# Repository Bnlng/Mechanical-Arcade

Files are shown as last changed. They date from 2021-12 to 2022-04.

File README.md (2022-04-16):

<h1>Mechanical Dogfight</h1>
<h3>Von Ben und Martin, 12bc</h3>

<h2>Inhaltsverzeichnis</h2>

<ul style="list-stlye-type:none">
    <li><a href="#einl">1. Einleitung</a></li>
    <li><a href="#proj">2. Das Projekt</a></li>
    <li><a href="#hard">3. Hardware</a></li>
    <ul>
        <li><a href="#aufb">3.1 Aufbau</a></li>
        <li><a href="#teil">3.2 Verwendete Bauteile</a></li>
        <li><a href="#schalt">3.3 Schaltplan</a></li>
    </ul>
    <li><a href="#soft">2. Software</a></li>
</ul>

<h2 id="einl">Einleitung</h2>

Dies ist die Projektseite für unser Informatikprojekt des ersten Halbjahres. Uns war von Anfang an klar, dass wir etwas im Bereich des Physical Computing machen wollen. Als wir einen alten Joystick aus den 90er Jahren auf dem Dachboden gefunden hatten sind wir auf die Idee für dieses Projekt gekommen und waren sofort begeistert. Wir haben uns dazu entschieden, das Projekt auf der Arduino Plattform umzusetzen, da diese recht einsteigerfreundlich und Perfekt für Projekte wie dieses geeignet ist.
    
<h2 id="proj">Das Projekt</h2>

"Mechanical Dogfight" ist ein Singleplayer Computerspiel auf Arduino-Basis, dessen Inhalt ein Luftkampf (engl. Dogfight) zwischen zwei Flugzeugen ist. Der Spieler steuert das Verfolgerflugzeug, eine englische Supermarine Spitfire, mit einem Joystick. Das Besondere an diesem Spiel ist, dass es sich nicht auf einem Bildschirm abspielt, sondern mit echten Modellen der Flugzeuge, welche sich zweidimensional im Spielekasten bewegen können. Das Gegnerflugzeug wird automatisch vom Arduino gesteuert und muss vom Spieler mittels des Bordgeschützes getroffen werden. Zurzeit ist nur das Flugzeug des Spielers fertiggestellt, daher handelt es sich bei diesem Projekt erst einmal nur um eine Art „Proof of Concept“. Alles funktioniert, wie gedacht, weshalb wir das Projekt als vollen Erfolg ansehen. Wer das Projekt in Bewegung sehen möchte kann es sich [hier](https://www.youtube.com/watch?v=7guUQbI5MUM) aus der Sicht des Spielers anschauen und [hier](https://www.youtube.com/watch?v=KiZhklhcncI) von hinten, wobei auch die Mechanik des Spiels zu sehen ist.



<h2 id="hard">Hardware</h2>

<h3 id="aufb">Aufbau</h3>

Damit das Flugzeug alle Punkte erreichen kann haben wir zweiachsiges mechanisches Bewegungssystem gebaut. Es basiert auf zwei Schlitten, welche sich jeweils waagerecht und senkrecht in Schienen bewegen. Die Bewegung wird durch zwei Getriebemotoren ermöglicht, welche die Rotation mittels Zahnräder und Zahnstangen in lineare Bewegung auf die Schlitten übertragen. Der komplette Aufbau für die senkrechte Bewegung ist auf dem Schlitten für die Waagerechte Bewegung montiert. Der Aufbau und die Funktion werden verständlicher bei Betrachtung des folgenden Bildes und des 3D-Modelles (zu öffnen mit 3D-Viewer, bei Windows 10 vorinstalliert).
 


Ein genaueres 3D Modell kann unter <code>3D Modell.3mf</code> in den Dateien des Repositorys eingesehen werden.

Außerdem findet sich [hier](https://www.youtube.com/watch?v=KiZhklhcncI) ein Vorführungsvideo aus der Ansicht von hinten, also vom späteren Inneren des Spielekastens. [Hier](https://www.youtube.com/watch?v=7guUQbI5MUM) findet sich ein Vorführungsvideo aus der Spieleransicht.

<h3 id="teil">Verwendete Bauteile</h3>

<h4>Netzteil 7-9V</h4>

Dieses versorgt den Arduino und die Motoren mit Strom. Der Arduino Nano benötigt eine Spannungsversorgung von 7 bis 12V um arbeiten zu können. Eine besonders hohe Leistung muss das Netzteil nicht aufweisen, da das gesamte Projekt noch keine Ströme über 1A gezogen hat.

<h4>Arduino</h4>

Arduino ist eine Open Source Physical-Computing-Plattform. Es handelt sich um einen Microcontroller mit mehreren analogen und digitalen Ein und Ausgängen. Dieser ist das Herzstück unseres Projektes und für die Verarbeitung der Steuersignale und später für das Steuern des Gegnerflugzeuges und das Punktezählen zuständig.

<h4>DC-Motor-Treiber</h4>
Hierbei handelt es sich um den L298N dual H-Bridge Driver. Dieser ermöglicht die Steuerung von zwei Gleichstrommotoren. Also die Änderung von Drehrichtung und Geschwindigkeit.

<h4>DC-Getriebemotoren</h4>

Diese sind für die Bewegung des Flugzeuges zuständig. Durch das Getriebe sind sie in der Lage deutlich mehr Drehmoment zu leisten. Dies ist für das Projekt notwendig, da die Motoren sonst nicht in der Lage wären auch nur eine Umdrehung zu machen.  

<h4>3D-Gedruckte Komponenten</h4>

Alle, im oben zu sehenden 3D-Modell schwarz gefärbten Komponenten sind mittels einem FDM Druckers aus PLA gefertigt worden. Die Hauptkomponenten sind die zwei Schlitten, auf denen die Motoren und das Flugzeug montiert sind, sowie die Zahnräder und Zahnstangen für die Kraftübertragung des Motors.  Die Teile wurden von uns selbst in dem CAD-Programm <I>Fusion 360</I> entwickelt.  Nur das Flugzeugmodell ist ein 3D-Scan aus dem Internet, jedoch musste hier die Einbettung für den Laserpointer in den Rumpf modelliert werden.

<h4>Schubladenschienen</h4>

Die Schienen, auf denen sich die Schlitten bewegen sind die äußeren Schienen von Kugelauszügen. Diese haben links und rechts an der Innenseite eine halbkreisförmige Nut. Diese Nuten bilden die einzige Kontaktfläche zwischen Schlitten und Schiene. Den inneren Teil des Kugelauszuges dienen zur Stabilisierung der Zahnstangen, welche aufgrund der Abmessungen in zwei Teilen gedruckt werden mussten.

<h4>Joystick</h4>

Bei dem Joystick handelt es sich um einen Logitech Wingman Extreme aus dem Jahre 1994. Die Ermittlung der Stellung erfolgt mittels zwei Drehpotentimetern, eines für die X-Achse und eines für die Y-Achse. Potentiometer sind Spannungsteiler. An zwei der drei Anschlüsse wird eine Spannung angelegt, an dem dritten Anschluss ist nun abhängig vom Winkel der Drehachse eine Spannung messbar. Diese Spannung dient dem Arduino als Inputwert für die Bewegung des Flugzeuges.

<h4>Taster</h4>

An jedes Ende der Bewegungsachsen ist ein Taster montiert, welcher gedrückt wird, wenn die Bewegungsschlitten an das Ende der Bewegungsachsen stoßen. Wir haben Taster mit Rollenhebel genutzt, da diese einen sehr weichen und progressiven Druckpunkt haben. Dies beugt Schäden am Material vor, wenn man mit hoher Geschwindigkeit gegen einen Taster fährt.

<h4>Weitere Bauteile</h4>

* 1k Ω Widerstände - Pull-Down widerstand für die Taster
* Ø4mm Aluminiumstange - Verbindung Flugzeug<->Y-Schlitten
* Multiplexplatten - Montageplatte (später Gehäuse)
* Steckbrett und Kabel - Aufbau der Elektrik

<h3 id="schalt">Schaltplan</h3>



<h4>Erklärung der Elektrik</h4>

**Spannungsversorgung:**
Der Arduino und die Motoren werden mit einer Spannung von mind. 7V vom Netzteil versorgt. Die Arbeitsspannung für In- und Outputsignale liegt bei 5V. Hierzu hat der Arduino Nano einen Spannungswandel verbaut. Die Potentiometer und Taster sind also an den 5V Pin des Arduinos angeschlossen. 

**Endtaster:**
Den Tastern ist jeweils ein 1k Ω Widerstand als Pull-Down Widerstand vorgeschaltet. Diese sind notwendig, damit 1. das Spannungsniveau des Inputpins bei nicht Betätigung des Tasters bei Ground also 0 liegt und 2. damit bei Betätigung kein zu hoher Strom fließt.

**Joystick:**
Die zwei Joysticks sind parallel geschaltet und die Outputpins sind an den Arduino Inputpins A0 und A1 angeschlossen.

**Motor Treiber:** 
Das Motortreiber Board L298N wird vom Netzteil mit Spannung versorgt. Die Motoren sind an diesem Board angeschlossen. Zu jedem Motor gehören zwei Inputleitungen, welche jeweils an einen PWM-Outputpin des Arduinos angeschlossen sind. Liegt auf der einen Leitung eines Input-Paares eine Spannung zwischen 0 und 5V an, so dreht sich de Motor in die eine Richtung, wenn auf der anderen Leitung eine Spannung anliegt in die andere Richtung. Die Spannung, die an den Motor geht ist proportional zur Inputspannung. Wenn die Inputspannung an das Treiberborad 1,5V , also 30% von 5V, beträgt, so wird die Outputspannung an den Motor 30% von der Betriebsspannung des Treiberborads betragen, also 30% von 7V. 

**Anmerkungen:** Da es in der verwendeten Software (TinkerCAD) keinen Joystick gab wird dieser durch zwei Potentiometer dargestellt was technisch gesehen genau das gleiche ist. Die Pins des Motor-Controllers müssen je nach Controller anders belegt werden.

<h2 id="soft">Software</h2>

Die Programmiersprache von Arduino basiert auf c++, verfügt aber über zusätzliche befehle, genaueres über die Sprache kann [hier](https://www.arduino.cc/reference/de/) nachgelesen werden. Der gesamte Sketch wird im Folgenden Schritt für Schritt erklärt, kann aber auch in den Dateien des Repositorys [ohne Erklärungen](https://github.com/Bnlng/Mechanical-Dogfight/blob/main/Arduino%20Code%20ohne%20Erkl%C3%A4rungen.ino) und [mit Erklärungen](https://github.com/Bnlng/Mechanical-Dogfight/blob/main/Arduino%20Code%20mit%20Erkl%C3%A4rungen.ino) eingesehen und heruntergeladen werden.

<details>
    <summary>Gesamter Sketch</summary>

```c
//Arduino Pins
const int joystickXInputPin = A1;
const int joystickYInputPin = A0;

const int posXpwmPin = 10;
const int negXpwmPin = 6;
const int posYpwmPin = 9;
const int negYpwmPin = 11;

const int buttonLeftPin = 2;
const int buttonRightPin = 4;
const int buttonTopPin = 7;
const int buttonBottomPin = 8;

//Joystick callibration
int joystickXMaxValue = 955;
int joystickXMinValue = 210;
int joystickXCenterValue = 511;
int joystickXCenterTollerance = 20;

int joystickYMaxValue = 890;
int joystickYMinValue = 155;
int joystickYCenterValue = 512;
int joystickYCenterTollerance = 20;

int sensorValueX = 0;
int sensorValueY = 0;

int outputValueX = 0;
int outputValueY = 0;

int buttonLeftState = 0;
int buttonRightState = 0;
int buttonTopState = 0;
int buttonBottomState = 0;

void setup() {
    Serial.begin(9600);

    pinMode(buttonLeftPin, INPUT);
    pinMode(buttonRightPin, INPUT);
    pinMode(buttonTopPin, INPUT);
    pinMode(buttonBottomPin, INPUT);
}

void loop() {
    buttonLeftState = digitalRead(buttonLeftPin);
    buttonRightState = digitalRead(buttonRightPin);
    buttonTopState = digitalRead(buttonTopPin);
    buttonBottomState = digitalRead(buttonBottomPin);

    //X-movement
    sensorValueX = analogRead(joystickXInputPin);

    if (sensorValueX > (joystickXCenterValue + joystickXCenterTollerance) && buttonLeftState == LOW) {
        outputValueX = map(sensorValueX, joystickXCenterValue + joystickXCenterTollerance, joystickXMaxValue, 0, 255); 
        analogWrite(negXpwmPin, 0);
        analogWrite(posXpwmPin, outputValueX);
    }
    else if (sensorValueX < (joystickXCenterValue - joystickXCenterTollerance) && buttonRightState == LOW) {
        outputValueX = map(sensorValueX, joystickXCenterValue - joystickXCenterTollerance, joystickYMinValue, 0, 255);
        analogWrite(posXpwmPin, 0);
        analogWrite(negXpwmPin, outputValueX);
    }
    else{
        outputValueX = 0;
        analogWrite(posXpwmPin, outputValueX);
        analogWrite(negXpwmPin, outputValueX);
    }

    //Y-movement
    sensorValueY = analogRead(joystickYInputPin);

    if (sensorValueY > (joystickYCenterValue + joystickYCenterTollerance) && buttonTopState == LOW) {
        outputValueY = map(sensorValueY, joystickYCenterValue + joystickYCenterTollerance, joystickYMaxValue, 0, 255);
        analogWrite(negYpwmPin, 0);
        analogWrite(posYpwmPin, outputValueY);
    }
    else if (sensorValueY < (joystickYCenterValue - joystickYCenterTollerance) && buttonBottomState == LOW) {
        outputValueY = map(sensorValueY, joystickYCenterValue - joystickYCenterTollerance, joystickYMinValue, 0, 255);
        analogWrite(posYpwmPin, 0);
        analogWrite(negYpwmPin, outputValueY);
    }
    else{
        outputValueY = 0;
        analogWrite(posYpwmPin, outputValueY);
        analogWrite(negYpwmPin, outputValueY);
    }
    
    Serial.println("sensorX = ");
    Serial.print(sensorValueX);
    Serial.print("\t outputX = ");
    Serial.print(outputValueX);

    Serial.print("\tsensorY = ");
    Serial.print(sensorValueY);
    Serial.print("\t outputY = ");
    Serial.print(outputValueY);
    
    delay(1);
}
```
                                        
</details>

<h3>Schritt für Schritt Erklärung</h3>

<h4>1. Pins definieren</h4>

Als allererstes wird in Variablen gespeichert, welche Pins am Arduino für was zuständig sind. Die Pins A1 und A2 lesen die zwei verschiedenen Achsen des Joysticks aus, dabei wird pro Achse ein Wert von 0 bis 1023 ausgelesen. In der Ausgangsposition ist dieser Wert ca. 512 und wenn der Joystick beispielsweise nach oben gedrückt wird, kann dieser Wert je nach Stellung zwischen 513 und 1023 sein.

Als nächstes werden den verschiedenen Bewegungsrichtungen des Flugzeugs Pins zugewiesen, wenn diese Pins aktiviert werden, gibt der Arduino ein PWM Signal ([mehr Infos](https://www.arduino.cc/en/Tutorial/Foundations/PWM)) über diesen Pin aus, der Motor-Controller lässt daraufhin den Motor (X- oder Y-Achse) in eine bestimmte Richtung drehen. Soll sich die Drehrichtung ändern muss der Pin ausgeschaltet und ein anderer angeschaltet werden. `posXpwmPin` bewegt das Flugzeug nach rechts, `negXpwmPin` nach links, `posYpwmPin` nach oben und `negYpwmPin` nach unten. Die Bennenung ist analog zum Koordinatensystem aus der Mathematik.

Danach werden die Pins für die Taster am Rand des Spiels definiert. Wird ein Taster gedrückt, so liest der dazugehörige Pin HIGH aus, wird er nicht gedrückt, dann LOW.

```c
//Input Pins um den Joystick auszulesen
const int joystickXInputPin = A1; //X-Achse des Joysticks
const int joystickYInputPin = A0; //Y-Achse des Joysticks

//PWM pins für den Motor-Controller
const int posXpwmPin = 10; //rechts
const int negXpwmPin = 6; //links
const int posYpwmPin = 9; //oben
const int negYpwmPin = 11; //unten

//Pins für die Taster an den Rändern des Spiels 
const int buttonLeftPin = 2; //links
const int buttonRightPin = 4; //rechts
const int buttonTopPin = 7; //oben
const int buttonBottomPin = 8; //unten
```

<h4>2. Joystick Kalibrierung</h4>

Da der Joystick nicht perfekt ist gibt er in der Ausgangsposition nicht genau 512 aus und bei voller Betätigung weder 0 noch 1023, deshalb muss jeder Joystick individuell kalibriert werden. Dazu müssen über den Seriellen Motor des Arduinos die Output-Werte des Joysticks ausgelesen werden. Die Werte, die in der Ausgangsstellung ausgegeben werden müssen bei `joystickXCenterValue` und `joystickYCenterValue` eingetragen werden. Anschließen müssen die maximalen und minimalen Werte, die der Joystick ausgibt, wenn er so stark wie möglich gedrückt wird in die dafür vorgesehenen Variablen eingetragen werden.

```c
//Joystick Kalibrierung
int joystickXMaxValue = 955; //Maximaler X-Wert, den der Joystick ausgibt
int joystickXMinValue = 210; //Minimaler X-Wert, den der Joystick ausgibt
int joystickXCenterValue = 516; //X-Wert, den der Joystick in der Ausgangsposition ausgibt
int joystickXCenterTollerance = 6; //Toleranz für die Ausgangsposition des Joyticks auf der X-Achse

int joystickYMaxValue = 890; //Maximaler Y-Wert, den der Joystick ausgibt
int joystickYMinValue = 155; //Minimaler Y-Wert, den der Joystick ausgibt
int joystickYCenterValue = 522; //Y-Wert, den der Joystick in der Ausgangsposition ausgibt
int joystickYCenterTollerance = 12; //Toleranz für die Ausgangsposition des Joyticks auf der Y-Achse
```

<h4>3. Zwischenspeicher Variablen</h4>
    
Dies sind die Variablen, in denen Werte im loop (der Teil des Sketches, der immer wieder wiederholt wird) zwischengespeichert werden. Die Funktionen der Variablen werden im Code-Bock beschrieben.

```c
//Variablen um die Ausgabewerte (0-1023) des Joysticks im loop zwischenzuspeichern
int sensorValueX = 0;
int sensorValueY = 0;

//Variablen um die für den Motor-Controller konvertierten Ausgabewerte (0-255) des Joysticks im loop zwischenzuspeichern
int outputValueX = 0;
int outputValueY = 0;

//Variablen um den Status (HIGHT oder LOW) der Taster an den Rändern zwischenzuspeichern 
int buttonLeftState = 0;
int buttonRightState = 0;
int buttonTopState = 0;
int buttonBottomState = 0;
```

<h4>4. Setup</h4>

Dieser Teil des Sketches wird nur ein einziges Mal beim Starten des Arduinos ausgeführt. `Serial.begin(9600);` Legt die Datenrate in Bit pro Sekunde (Baud) für die serielle Datenübertragung fest und macht das Anzeigen von Daten über den Seriellen Monitor möglich. `pinMode(Pin, INPUT);` legt den Pin als Input fest.

```c
void setup() {
    Serial.begin(9600); (für die Kalibrierung des Joysticks notwendig)

    pinMode(buttonLeftPin, INPUT);
    pinMode(buttonRightPin, INPUT);
    pinMode(buttonTopPin, INPUT);
    pinMode(buttonBottomPin, INPUT);
}
```

<h4>5. loop</h4>

Alles innerhalb der geschwungenen Klammern von `void loop() {}` wird immer wieder ausgeführt. Um die Funktionsweise besser erklären zu können ist der loop in verschiedene Abschnitte gegliedert.

Als erstes werden die Taster ausgelesen und deren Zustand zwischengespeichert.

```c
void loop() {
    buttonLeftState = digitalRead(buttonLeftPin);
    buttonRightState = digitalRead(buttonRightPin);
    buttonTopState = digitalRead(buttonTopPin);
    buttonBottomState = digitalRead(buttonBottomPin);
```

Der Code in den nächsten Drei Abschnitten ist für die Bewegung des Flugzeugs auf der X-Achse zuständig. Zunächst wird der Ausgabewert des Joysticks für die X-Achse ausgelesen und gespeichert. Danach wird `if() {}` verwendet, dabei wird überprüft, ob die in der Klammer stehende Bedingung erfüllt ist und falls dies so ist wird der Code zwischen den geschwungenen Klammern ausgeführt. Als Bedingung muss in unserem Fall der Output vom Joystick größer sein als er ist, wenn der Joystick in der Ausgangsposition ist und der Taster an der rechten Seite darf nicht betätigt sein. Zwischen den geschwungenen Klammern wird zunächst mit Hilfe der `map()`-Funktion der Ausgabewert des Joysticks in einen Wert zwischen 0 und 255 konvertiert. Anschließend wird über `analogWrite(Pin, 0-255)` die Geschwindigkeit des Motors nach links (falls vorhanden) auf null und die Geschwindigkeit nach Rechts auf den eben konvertierten Wert gesetzt. 0 entspricht stillstand und 255 voller Geschwindigkeit.

```c
    sensorValueX = analogRead(joystickXInputPin); //Liest den Ausgabewert des Joysticks für die X-Achse aus und speichert diesen zwischen

    if (sensorValueX > (joystickXCenterValue + joystickXCenterTollerance) && buttonLeftState == LOW) {
        outputValueX = map(sensorValueX, joystickXCenterValue + joystickXCenterTollerance, joystickXMaxValue, 0, 255);
        analogWrite(negXpwmPin, 0); //Setzt die Geschwindigkeit des Motors nach links auf Null
        analogWrite(posXpwmPin, outputValueX); //Übermittelt die Geschwindigkeit nach rechts an den Motor-Controller
    }
```

`else if()` ist wie `if()`, allerdings wird es nur ausgeführt, wenn die Bedingung von `if()` davor nicht erfüllt wurde. Die Bedingung ist diesmal ähnlich wie die davor, nur ist Alles invertiert, d.h., dass nicht die Bewegung nach rechts geregelt wird, sondern die nach Links.

```c
    else if (sensorValueX < (joystickXCenterValue - joystickXCenterTollerance) && buttonRightState == LOW) { //Wenn der Joystick auf der X-Achse links von der Mitte ist und der Taster auf der linken Seite nicht betätigt ist, dann:
        outputValueX = map(sensorValueX, joystickXCenterValue - joystickXCenterTollerance, joystickYMinValue, 0, 255); //Konvertiert den Ausgabewert des Joysticks in eine Geschwindigkeit für den Motor-Controller
        analogWrite(posXpwmPin, 0); //Setzt die Geschwindigkeit des Motors nach rechts auf Null
        analogWrite(negXpwmPin, outputValueX); //Übermittelt die Geschwindigkeit nach links an den Motor-Controller
    }
```

Abschließend wird eine Else-Anweisung verwendet, diese führt den Code in den Geschwungenen Klammern nur aus, wenn die beiden Bedingungen davor nicht erfüllt wurden. Der Code setzt die Geschwindigkeit des Motors (falls vorhanden) in beide Richtungen auf null.

```c
    else{ //Wenn der Joystick in der Ausgangsposition ist, dann:
        outputValueX = 0; //setzt Variable für die Motorgeschwindigkeit auf 0

        //Übermittelt die Geschwindigkeiten an den Motor-Controller
        analogWrite(posXpwmPin, outputValueX);
        analogWrite(negXpwmPin, outputValueX);
    }
```

<details>
    <summary>Das Gleiche für die Y-Achse</summary>

```c
    //Y-movement
    sensorValueY = analogRead(joystickYInputPin); //Liest den Ausgabewert des Joysticks für die Y-Achse aus und speichert diesen zwischen

    if (sensorValueY > (joystickYCenterValue + joystickYCenterTollerance) && buttonTopState == LOW) {  //Wenn der Joystick auf der Y-Achse oberhalb der Mitte ist und der Taster oben nicht betätigt ist, dann:
        outputValueY = map(sensorValueY, joystickYCenterValue + joystickYCenterTollerance, joystickYMaxValue, 0, 255); //Konvertiert den Ausgabewert des Joysticks in eine Geschwindigkeit für den Motor-Controller
        analogWrite(negYpwmPin, 0); //Setzt die Geschwindigkeit des Motors nach unten auf Null
        analogWrite(posYpwmPin, outputValueY); //Übermittelt die Geschwindigkeit nach oben an den Motor-Controller
    }
    else if (sensorValueY < (joystickYCenterValue - joystickYCenterTollerance) && buttonBottomState == LOW) {  //Wenn der Joystick auf der Y-Achse unterhalb der Mitte ist und der Taster unten nicht betätigt ist, dann:
        outputValueY = map(sensorValueY, joystickYCenterValue - joystickYCenterTollerance, joystickYMinValue, 0, 255); //Konvertiert den Ausgabewert des Joysticks in eine Geschwindigkeit für den Motor-Controller
        analogWrite(posYpwmPin, 0); //Setzt die Geschwindigkeit des Motors nach oben auf Null
        analogWrite(negYpwmPin, outputValueY); //Übermittelt die Geschwindigkeit nach unten an den Motor-Controller
    }
    else{
        outputValueY = 0; //setzt Variable für die Motorgeschwindigkeit auf 0

        //Übermittelt die Geschwindigkeiten an den Motor-Controller
        analogWrite(posYpwmPin, outputValueY);
        analogWrite(negYpwmPin, outputValueY);
    }
```

</details>

<h4>6. Output für den Plotter</h4>

Als allerletztes werden verschiedene Werte an den Seriellen Monitor übermitteltelt. Dies wird nur zur Kaliebrirung des Joysticks und zur Fehlerbehebung benötigt.

```c
    //Output für den Plotter (für die Kallibrierung)
    Serial.println("sensorX = ");
    Serial.print(sensorValueX);
    Serial.print("\t outputX = ");
    Serial.print(outputValueX);

    Serial.print("\tsensorY = ");
    Serial.print(sensorValueY);
    Serial.print("\t outputY = ");
    Serial.print(outputValueY);

    delay(1);
}
```

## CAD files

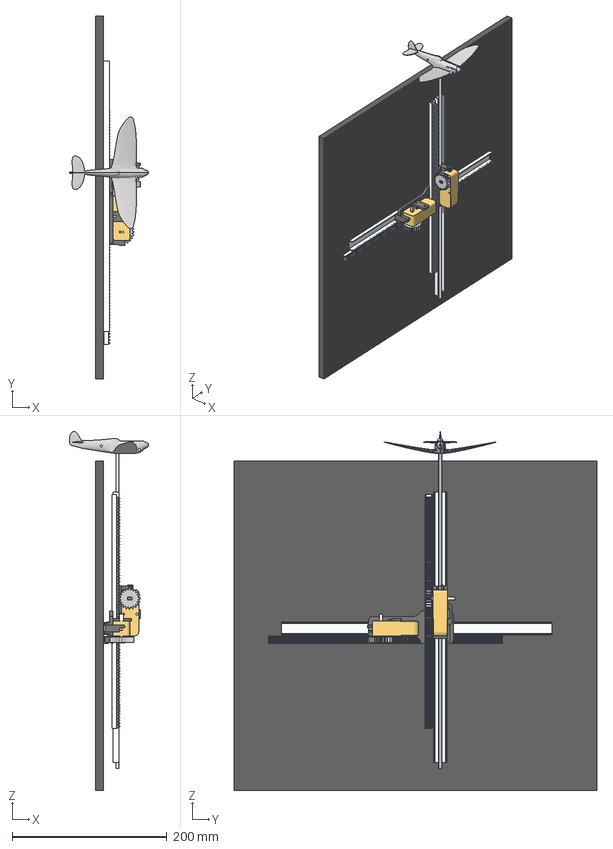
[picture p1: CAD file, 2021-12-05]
3D Modell.3mf
102.7 x 469.9 x 465.1 mm
Körper1 x 15
Körper2 x 2
Körper3
Körper4 x 3
Körper5
Körper7

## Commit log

2021-12-05 Create Arduino Code
2021-12-05 Update Arduino Code
2021-12-05 Update Arduino Code.ino
2021-12-05 Rename Arduino Code.ino to Arduino Code ohne Erklärungen.ino
2021-12-05 Update Arduino Code ohne Erklärungen.ino
2021-12-06 Update Arduino Code mit Erklärungen.ino
